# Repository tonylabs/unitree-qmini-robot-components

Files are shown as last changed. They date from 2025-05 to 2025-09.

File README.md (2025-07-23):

# Unitree Qmini Robot Resources

## 说明

这里不是 Unitree Qmini 机器人的官方 Git 资源库，点击[这里](https://github.com/unitreerobotics/Qmini) 访问官方 Repo.

本仓库包含了**修改**后 Unitree Qmini 机器人打印件，例如将部分螺丝孔位增加了倒角，减少不必要的打印支撑。和其他改装件，和部分为 Qmini 专门设计的 PCB。

### 站立支架

#### 所需材料

- [2040 铝合金型材 x 5](https://www.misumi.com.cn/vona2/detail/110310158399/?ProductCode=LCFB6-2040-200-TPW) 长度最短不小于100mm，两端加工螺纹。
- [M6 x 25mm x 20](https://item.taobao.com/item.htm?id=596366591280&skuId=4312388615153)
- M3 x 14 x 8
- M3 螺母 x 8

## Qmini 结构

```mermaid
flowchart TD
    subgraph "Qmini Robot"
        Body["Base Link"]
        %% Left Leg (LL)
        LL_HipYaw["LL Hip Yaw"]
        LL_HipRoll["LL Hip Roll"]
        LL_HipPitch["LL Hip Pitch"]
        LL_Knee["LL Knee"]
        LL_Ankle["LL Ankle"]
        
        %% Right Leg (RL)
        RL_HipYaw["RL Hip Yaw"]
        RL_HipRoll["RL Hip Roll"]
        RL_HipPitch["RL Hip Pitch"]
        RL_Knee["RL Knee"]
        RL_Ankle["RL Ankle"]
        
        %% Left Leg Connections
        Body --> LL_HipYaw
        LL_HipYaw --> LL_HipRoll
        LL_HipRoll --> LL_HipPitch
        LL_HipPitch --> LL_Knee
        LL_Knee --> LL_Ankle
        
        %% Right Leg Connections
        Body --> RL_HipYaw
        RL_HipYaw --> RL_HipRoll
        RL_HipRoll --> RL_HipPitch
        RL_HipPitch --> RL_Knee
        RL_Knee --> RL_Ankle
    end
```

### How to use the qmini_description

1. Navigate to your workspace:

```bash
$ sudo apt-get install python3-colcon-common-extensions
$ pip install catkin_pkg
$ cd /home/ubuntu/Documents/GitHub/unitree-qmini-robot-components/qmini_description
```

2. Build the package:

```bash
$ colcon build --packages-select qmini_description
```

3. Source the workspace:

```bash
$ source install/setup.bash
```

4. Launch the robot description:

```bash
$ ros2 launch qmini_description view_qmini.launch.py
```

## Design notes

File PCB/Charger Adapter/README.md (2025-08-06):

## Charger Adapter for Qmini Robot

### BOM

- J1, J2: [XT60PW-M](https://item.taobao.com/item.htm?id=934094991009&skuId=5824271752085)
- J3: [PJ-202A](https://item.taobao.com/item.htm?id=696211501043)
- J4, J5: [HF-B01M-11P-R1-A](https://item.taobao.com/item.htm?id=779219267835)
- C1~C4: 100uF 25V 6.3 x 5.4mm
- D1: [SMCJ45A](https://item.taobao.com/item.htm?id=608465785790)
- M1~M4: [SMTSO-M3-1.5ET](https://item.taobao.com/item.htm?id=626464596047&skuId=4448515665378)

### PCB Manufacturer

- Board Dimensions: 8.90 cm x 4.30 cm
- Board Thickness: 1.6mm ~ 2mm

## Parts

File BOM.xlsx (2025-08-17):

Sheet: 3D Print
 | Material | Infill | Insert | Printing Hours | Price
BODY
Battery Pack Bottom | ABS-HF | 15% |  | 13 | ¥0.00
Battery Pack 电池仓 | ABS-HF | 15% | M4 (6x6) x 8 | 35 | ¥0.00
Frame Core | Polymaker HT-PLA | 20% | M4 x 10 | M3 x 4 | 72 | ¥0.00
Frame Front Bottom 前端风扇安装件 | Polymaker HT-PLA | 100% | M3 x 6 | 0 | ¥0.00
Frame Top | Polymaker HT-PLA | 20% | M5 x 4 |  | ¥0.00
Handle |  |  |  |  | ¥0.00
Neck Actuator Mount | ABS-HF |  |  | 8 | ¥130.00
Raspberry Pi 4B Mount | ABS-HF |  |  | 6 | ¥0.00
Yaw Bottom Limit | ABS-HF |  |  | 2.1 | ¥0.00
Yaw Top | ABS-HF |  | M3 x 2 | 2.5 | ¥0.00
 |  |  |  |  | ¥0.00
 |  |  |  |  | ¥0.00
 |  |  |  |  | ¥0.00
 |  |  |  |  | ¥0.00
HIP
Hip Gear Left | Nylon 3201PA-F | 100% |  |  | ¥30.00
Hip Gear Right | Nylon 3201PA-F | 100% |  |  | ¥30.00
Hip Joint Roll Left | Nylon 3201PA-F | 100% |  |  | ¥178.00
Hip Joint Roll Right | Nylon 3201PA-F | 100% |  |  | ¥178.00
Hip Joint Mount Left | Resin-X | 40% | M4 x 4 | 13 | ¥38.00
Hip Joint Mount Right | Resin-X | 40% | M4 x 4 | 13 | ¥38.00
Hip Joint Yaw Left | Resin-X | 40% | M5 x 1 | 8 | ¥25.64
Hip Joint Yaw Right | Resin-X | 40% | M5 x 1 | 8 | ¥25.64
LEG
Lower Leg Right Cover | ABS-HF |  |  | 4.3 | ¥0.00
Lower Leg Right | ABS-HF / Nylon 3201PA-F |  |  | 9.4 | ¥353.00
Upper Leg Right Cover | ABS-HF |  |  | 11.55 | ¥0.00
Upper Leg Right | Resin-X |  |  | 0 | ¥126.89
Lower Leg Left Cover | ABS-HF |  |  | 4.3 | ¥0.00
Lower Leg Left | ABS-HF / Nylon 3201PA-F |  |  | 9.4 | ¥353.00
Upper Leg Left Cover | ABS-HF |  |  | 11.55 | ¥0.00
Upper Leg Left | Resin-X |  |  | 0 | ¥126.89
FOOT
Right Foot A | ABS-HF |  | M3 x 3 | 10.36 | ¥0.00
Right Foot B | ABS-HF |  |  | 5.4 | ¥0.00
Right Foot Pad 足底 | Resin |  |  | 0 | ¥145.00
Left Foot A | ABS-HF |  | M3 x 3 | 10.36 | ¥0.00
Left Foot B | ABS-HF |  |  | 5.4 | ¥0.00
Left Foot Pad 足底 | Resin |  |  | 0 | ¥145.00
PANEL
Panel Top Front | Resin-X | 100% | M3 x 2 | 0 | ¥198.00
Panel Top Rear | Resin-X | 100% |  | 0 | ¥143.00
Antenna Left | Resin-X | 100% |  |  | ¥24.00
Antenna Right | Resin-X | 100% |  |  | ¥24.00
 |  |  |  | 262.62 | ¥2312.06

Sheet: BOM
ITEM | SPECS | LINK | NOTES | QUANTITY | PRICE | SUBTOTAL
BODY
GO-M8010-6 | 24V | https://detail.tmall.com/item.htm?id=679335252560&skuId=5079135404284 |  | 11 | 550 | ¥6050.00
BODY
M5 热熔螺母 | M5 x 10 OD 7 | https://detail.tmall.com/item.htm?id=899448134936&skuId=5754304832006 | Frame Top | Hip Motor Mount | 4 | 0.15 | ¥0.60
M4 热熔螺母 | M4 x 10 OD 6 | https://detail.tmall.com/item.htm?id=899448134936&skuId=5798756972352 | Frame Top | Frame Core | Battery Pack | Hip Motor Mount | 28 | 0.2 | ¥5.60
M3 热熔螺母 | M3 x 4 OD 5 | https://item.taobao.com/item.htm?id=593581996419&skuId=4189077672129 | Frame Core | Front Bottom Fan Mount | IMU Mount | 12 | 0.2 | ¥2.40
不锈钢衬套 | Φ6 x 8 x 35 | https://detail.tmall.com/item.htm?id=822545298024&skuId=5702459126386 |  | 2 | 1.42 | ¥2.84
粒片螺丝 | M3.5 x 8 | https://item.taobao.com/item.htm?id=537967383377&skuId=3212738635362 | 髋关节电机安装座 | 顶部 YAW 轴电机 | 24 | 0.3 | ¥7.20
粒片螺丝 | M3.5 x 16 |  | 上身电机上盖底部限位 | 6 | 0.3 | ¥1.80
粒片螺丝 | M4 x 16 | https://item.taobao.com/item.htm?id=537967383377&skuId=5461813862733 | 髋关节电机安装座 | 8 | 0.3 | ¥2.40
FHCS 螺丝 | M4 x 12 平头 | https://item.taobao.com/item.htm?id=525468794969&skuId=3127568831102 | 摆驱动齿轮 | 12 | 0.3 | ¥3.60
SHCS 螺丝 | M4 x 12 杯头 | https://item.taobao.com/item.htm?id=525468794969&skuId=3127568831102 | 电机抱箍 | 4 | 0.3 | ¥1.20
SHCS 螺丝 | M4 x 16 杯头 | https://item.taobao.com/item.htm?id=529627939342&skuId=3165003331293 | 电池底部支撑件 | 机身上下主体 | 顶部 YAW 轴电机 | 侧摆电机 | 15 | 0.36 | ¥5.40
SHCS 螺丝 | M4 x 18 杯头 | https://item.taobao.com/item.htm?id=529627939342&skuId=3206368205626 | 电机抱箍 | 4 | 0.36 | ¥1.44
SHCS 螺丝 | M4 x 20 杯头 | https://item.taobao.com/item.htm?id=529627939342&skuId=3200246575353 | 主骨架与电池仓连接 | 前端风扇安装件 | 6 | 0.36 | ¥2.16
SHCS 螺丝 | M4 x 25 杯头 | https://item.taobao.com/item.htm?id=529627939342&skuId=3165003331294 | 机身上下主体 | 9 | 0.48 | ¥4.32
SHCS 螺丝 | M3 x 10 杯头 | https://item.taobao.com/item.htm?id=38977230812&skuId=3165007311199 | 4010 DC Fan | 4 | 0.28 | ¥1.12
SHCS 螺丝 | M3 x 14 杯头 | https://item.taobao.com/item.htm?id=38977230812&skuId=3165007311200 | 4010 DC Fan | 4 | 0.28 | ¥1.12
平面滚针轴承 | BA0619 | https://detail.tmall.com/item.htm?id=625077079266&skuId=5611160825675 | Frame Core | 2 | 3 | ¥6.00
636ZZ 轴承 | 6 x 22 x 7 | https://item.taobao.com/item.htm?id=652062390391&skuId=4698920756210 | Frame Core | 侧摆 | 4 | 6.5 | ¥26.00
塞打螺栓 | ￠6 x M5 x 16 | https://detail.tmall.com/item.htm?id=610905186565&skuId=5148221219880 | Frame Core | 2 | 1.062 | ¥2.12
塞打螺栓 | ￠6 x M5 x 55 | https://detail.tmall.com/item.htm?id=610905186565&skuId=4925270516930 | 侧摆 | 2 | 1.585 | ¥3.17
垫片 | 5.2 x D10 x 2 黑色 | https://item.taobao.com/item.htm?id=667085311743&skuId=4865635364512 | 侧摆 | 2 | 0.46 | ¥0.92
船形开关 | KCD1-104 | https://item.taobao.com/item.htm?id=577536722051 | 2档 | 1 | 1.12 | ¥1.12
轴流风扇 | 4010 24V DC | https://item.taobao.com/item.htm?id=611636440997&skuId=4310799149744 |  | 2 | 8 | ¥16.00
USB 转 485 | 四通道 | https://detail.tmall.com/item.htm?id=679335252560&skuId=5978377674682 |  | 1 | 199 | ¥199.00
动力线 | 16awg | https://detail.tmall.com/item.htm?id=679335252560&skuId=5136048959263 |  | 4 | 49 | ¥196.00
Raspberry Pi | 4B | https://detail.tmall.com/item.htm?id=679335252560&skuId=5079135404284 |  | 1 | 377 | ¥377.00
电池 | GO1-BT03 标准版 | https://detail.tmall.com/item.htm?id=654533678350&skuId=4892505606177 |  | 1 | 1999 | ¥1999.00
充电器 | GO1 | https://detail.tmall.com/item.htm?id=654533678350&skuId=5036835474357 |  | 1 | 600 | ¥600.00
IMU | N100 不带外壳 | https://detail.tmall.com/item.htm?id=645061129098&skuId=4648099525532 |  | 1 | 265 | ¥265.00
LEG
粒片螺丝 | M3.5 x 8 | https://item.taobao.com/item.htm?id=537967383377&skuId=3212738635362 | M8010 电机 | 50 | 0.3 | ¥15.00
粒片螺丝 | M3.5 x 12 | https://item.taobao.com/item.htm?id=537967383377&skuId=3212738635365 | 脚踝电机侧盖 | 50 | 0.3 | ¥15.00
SHCS 螺丝 | M4 x 16 杯头 | https://item.taobao.com/item.htm?id=529627939342&skuId=3165003331293 | 大、小腿连接 | 12 | 0.36 | ¥4.32
离心风扇 | 3010 24V DC 滚珠轴承 | https://item.taobao.com/item.htm?id=566323233973&skuId=5212591909140 |  | 4 | 16.5 | ¥66.00
动力线 | 16awg | https://detail.tmall.com/item.htm?id=679335252560&skuId=5136048959263 |  | 4 | 49 | ¥196.00
足端
M3 热熔螺母 | M3 x 7 OD 4.2 | https://detail.tmall.com/item.htm?id=899448134936&skuId=5922977711804 | Foot A | 6 | 0.2 | ¥1.20
SHCS 螺丝 | M3 x 25 杯头 | https://item.taobao.com/item.htm?id=38977230812&skuId=3200123895845 |  | 6 | 0.31 | ¥1.86
粒片螺丝或 FHCS 平头 | M4 x 16 | https://item.taobao.com/item.htm?id=537967383377&skuId=5461813862733 https://item.taobao.com/item.htm?id=525468794969&skuId=3127568831104 | 足端连接电机转轴 | 12 | 0.3 | ¥3.60
足底 |  |  | TPU 或柔性树脂 | 2 | 0 | ¥0.00
PANEL
M3 热熔螺母 | M3 x 7 OD 4.2 | https://detail.tmall.com/item.htm?id=899448134936&skuId=5922977711804 | Front Panel | 2 | 0.2 | ¥0.40
粒片螺丝 | M3.5 x 12 | https://item.taobao.com/item.htm?id=537967383377&skuId=3212738635365 | 顶盖 | 4 | 0.3 | ¥1.20
SHCS 螺丝 | M3 x 10 杯头 | https://item.taobao.com/item.htm?id=38977230812&skuId=3165007311199 | 天线 | 脸部 | 4 | 0.28 | ¥1.12
SHCS 螺丝 | M5 x 16 杯头 | https://item.taobao.com/item.htm?id=35431215248&skuId=3165685753062 | 提手 | 2 | 0.21 | ¥0.42
其他
波纹软管 |  |  |  | 1 | 5 | ¥5.00
站立支架
2040 型材 | 经济型欧标槽宽 6mm | https://www.misumi.com.cn/vona2/detail/110310158399/?ProductCode=LCFB6-2040-200-TPW |  | 5 | 13.19 | ¥65.95
BHCS 螺丝 | M6 x 25 | https://item.taobao.com/item.htm?id=596366591280&skuId=4312388615153 | 打印件连接 2040 型材 | 20 | 0.95 | ¥19.00
BHCS 螺丝 | M5 x 8 |  |  | 16 |  | ¥0.00
FHCS 螺丝 | M3 x 14 杯头 |  |  | 8 |  | ¥0.00
M3 螺母 |  |  |  | 8 |  | ¥0.00
 |  |  |  |  |  | ¥0.00
 |  |  |  |  |  | ¥0.00
 |  |  |  |  |  | ¥10180.60

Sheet: Wiring
连接 | 线径 | 长度 | 连接器 | 说明
大腿 | 16 AWG | 58cm | XT30(2+2) | 左电机 0 或右电机 0 连接至分电板
小腿 | 16 AWG | 25cm | XT30(2+2) | 左电机 1 或右电机 1 连接至左电机 2 或右电机 2

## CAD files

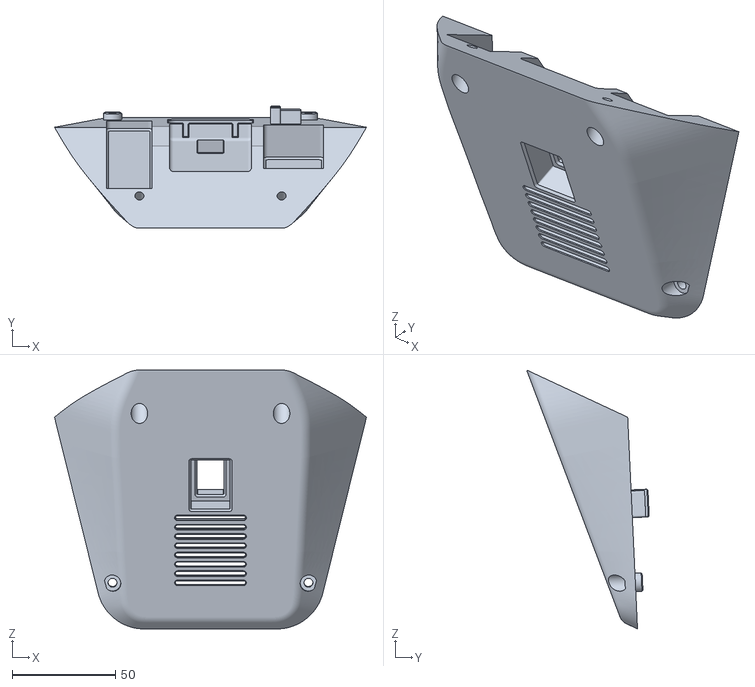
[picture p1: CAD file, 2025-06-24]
Print/Body/Battery Pack/DJI TB50-TB55/Battery Pack Bottom with 4010 Fan.stl
151.3 x 59.4 x 125.5

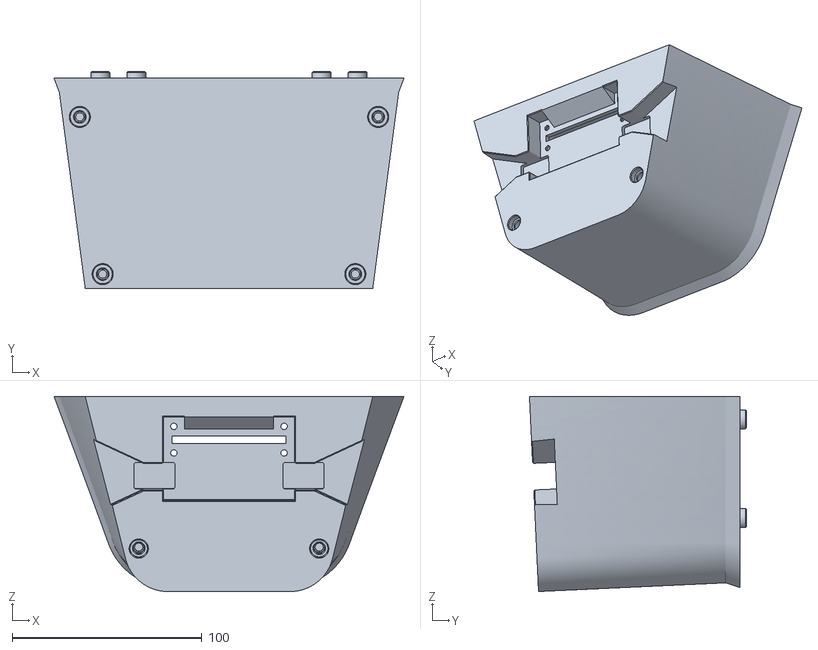
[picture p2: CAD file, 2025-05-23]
Print/Body/Battery Pack/GO1/Battery Pack GO1.stl
184.2 x 114.3 x 102.7

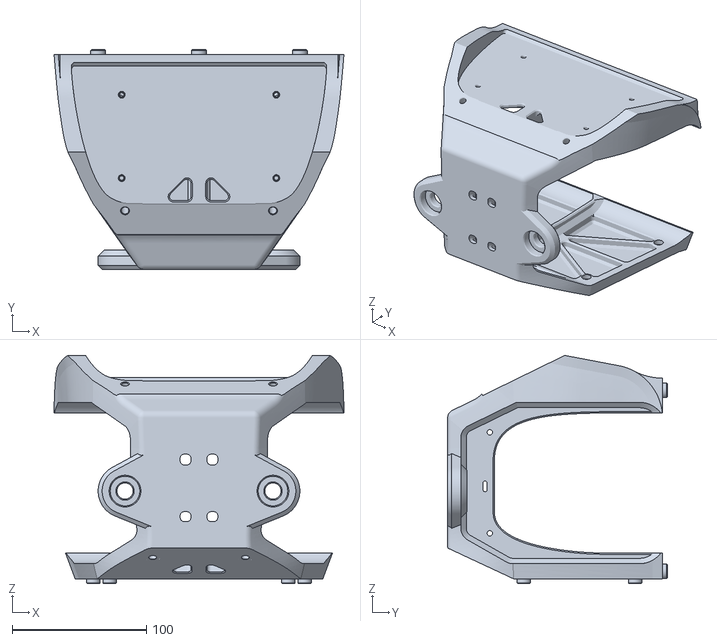
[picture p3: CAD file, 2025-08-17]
Print/Body/Frame Core.stl
215.6 x 163.3 x 169.7

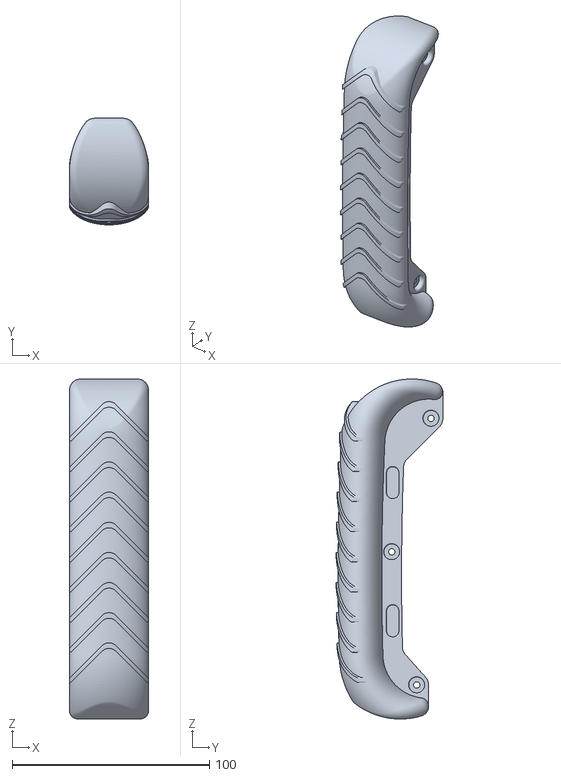
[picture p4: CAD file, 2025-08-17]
Print/Foot/Foot Pad x 2.stl
40.0 x 54.1 x 172.2

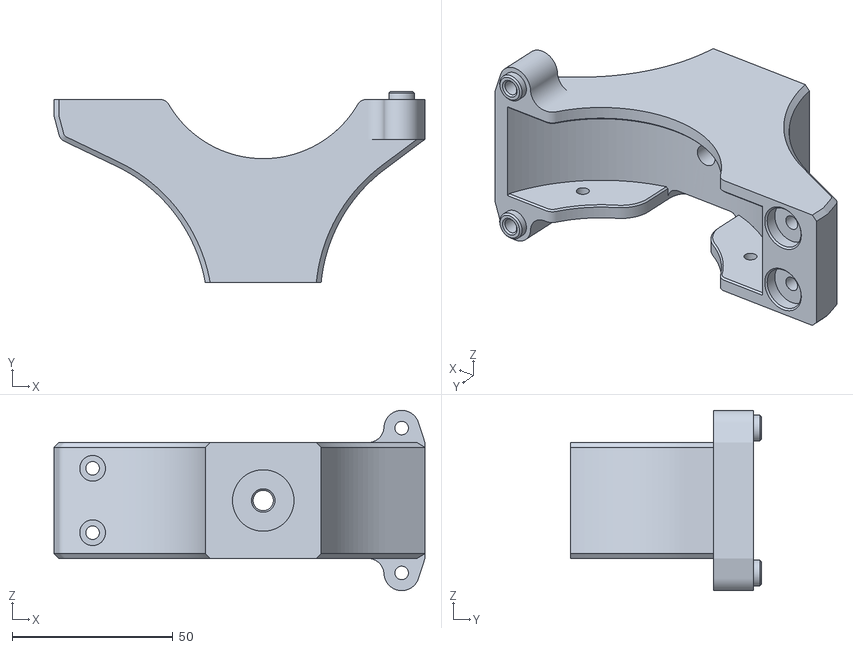
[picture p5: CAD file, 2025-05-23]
Print/Hip/Hip Joint Yaw Right.stl
115.2 x 59.4 x 56.0

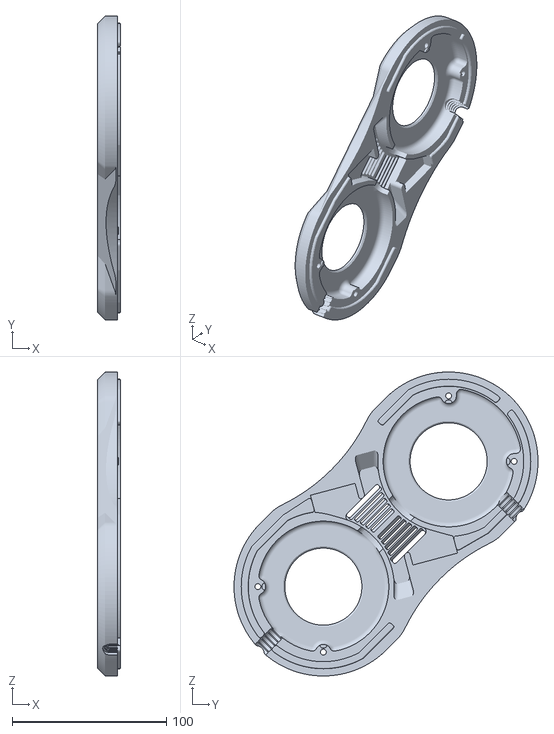
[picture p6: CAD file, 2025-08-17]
Print/Leg/Hollow - Upper Leg Right Cover.stl
15.0 x 197.3 x 197.3

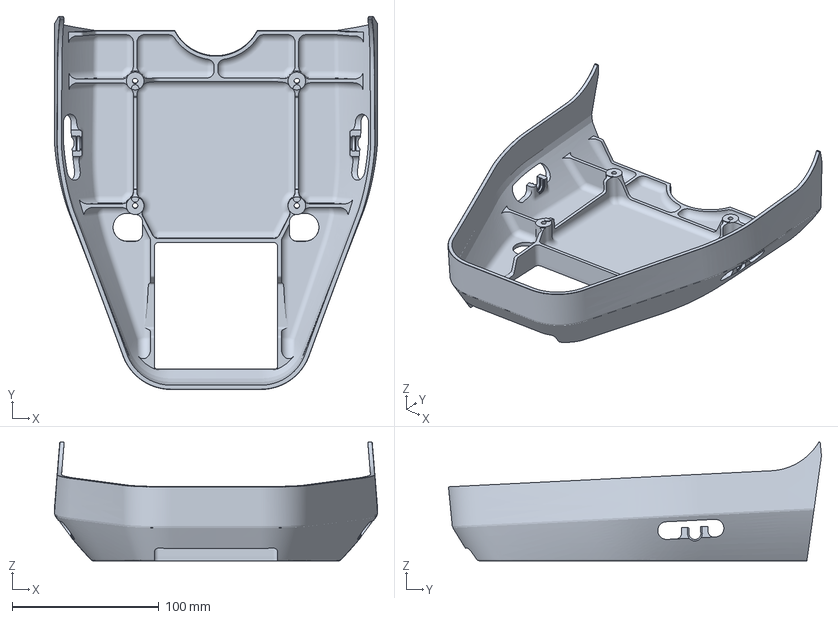
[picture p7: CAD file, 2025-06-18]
Print/Panel/Bambu Studio/Panel Top Rear.3mf
219.9 x 253.8 x 80.9 mm

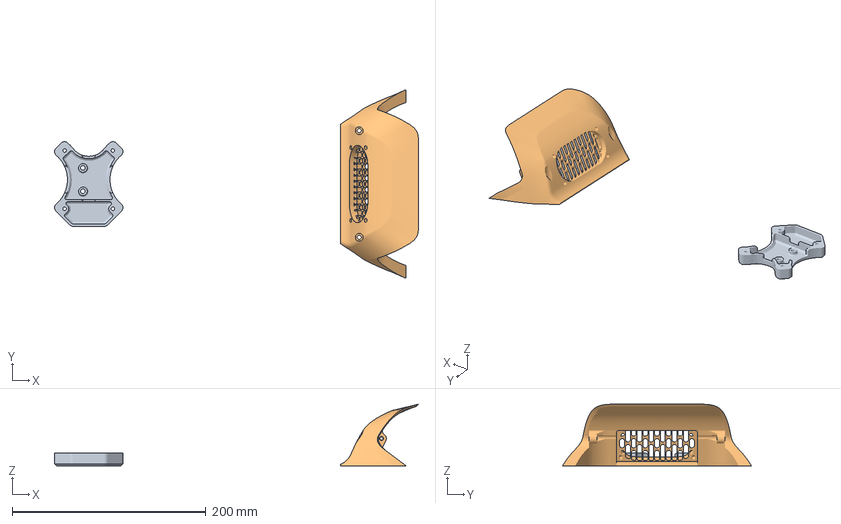
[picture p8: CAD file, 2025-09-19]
Print/Qmini - Bambu Studio.3mf
375.7 x 194.9 x 63.6 mm
Hip_Yaw_Top
Front Bottom

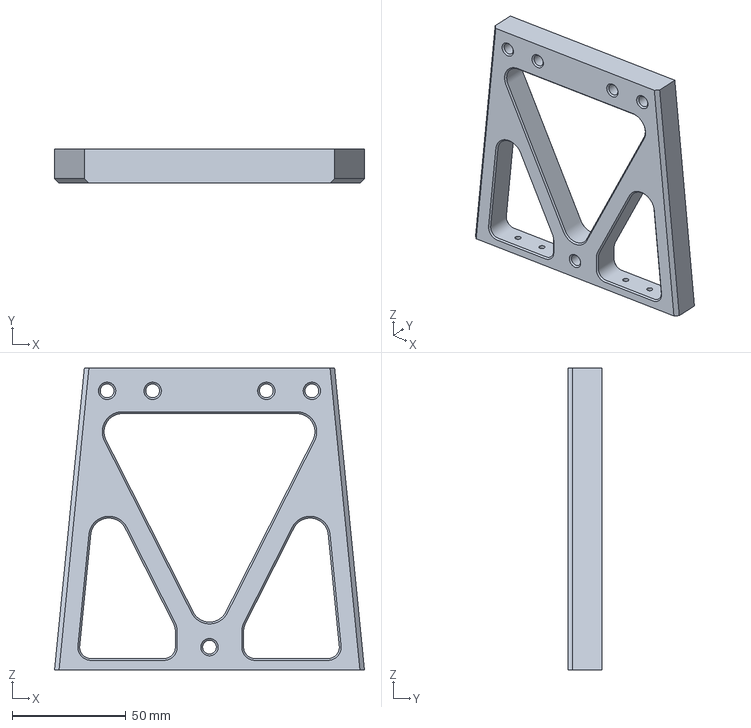
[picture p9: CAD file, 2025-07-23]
Print/Standing Frame/Standing Frame A x 2.3mf
136.1 x 15.0 x 132.6 mm

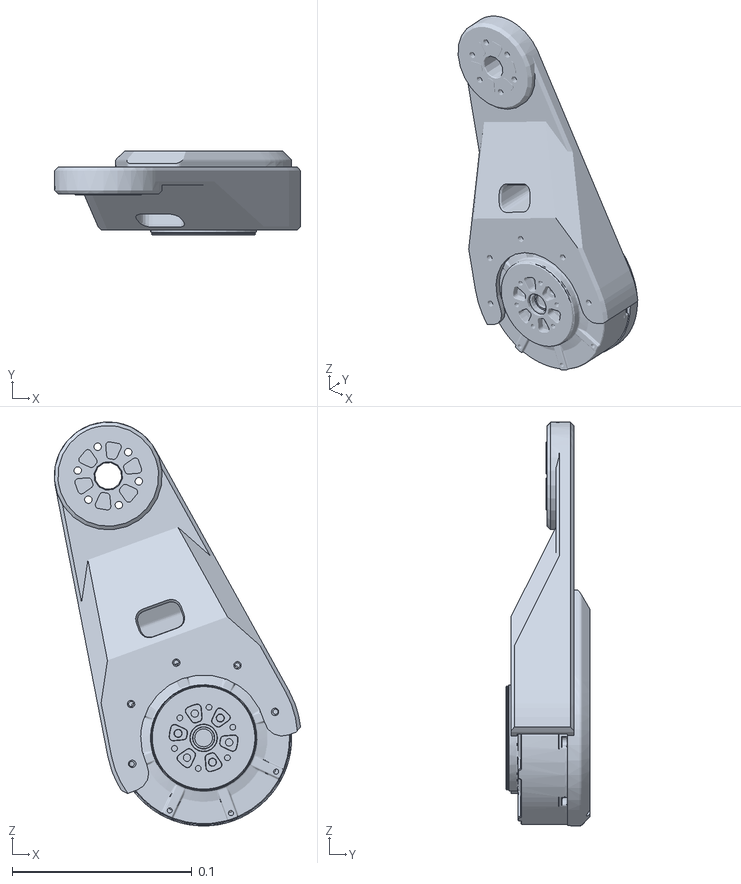
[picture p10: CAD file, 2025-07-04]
qmini_description/meshes/RL_knee.STL
0.137 x 0.0468 x 0.225

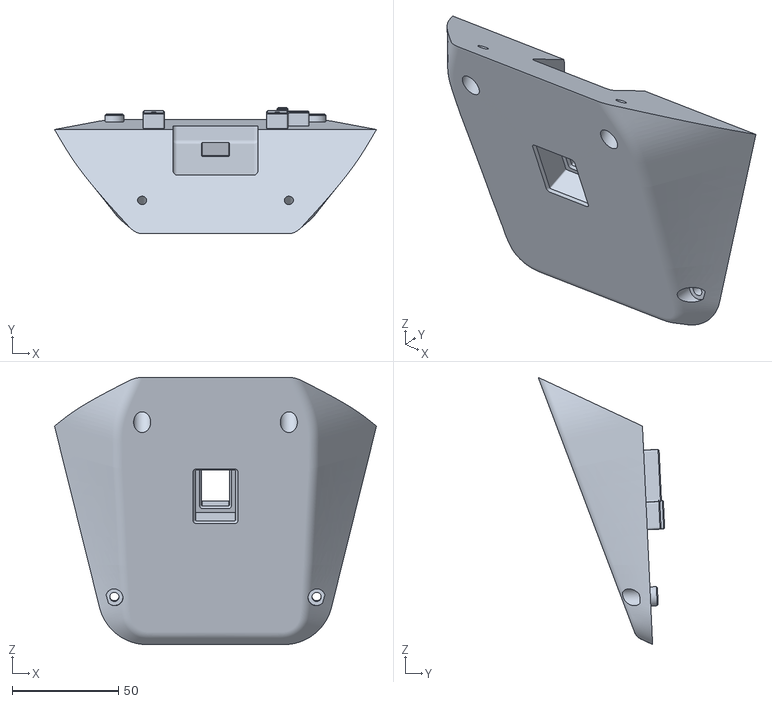
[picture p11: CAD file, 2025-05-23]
Print/Body/Battery Pack/GO1/Battery Pack Bottom GO1.stl
151.3 x 59.4 x 125.5

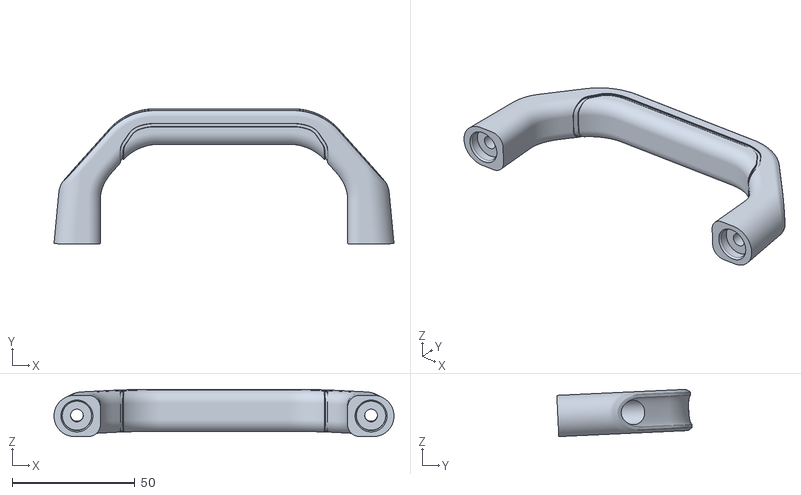
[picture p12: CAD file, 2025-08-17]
Print/Body/Handle.stl
138.7 x 55.2 x 19.3

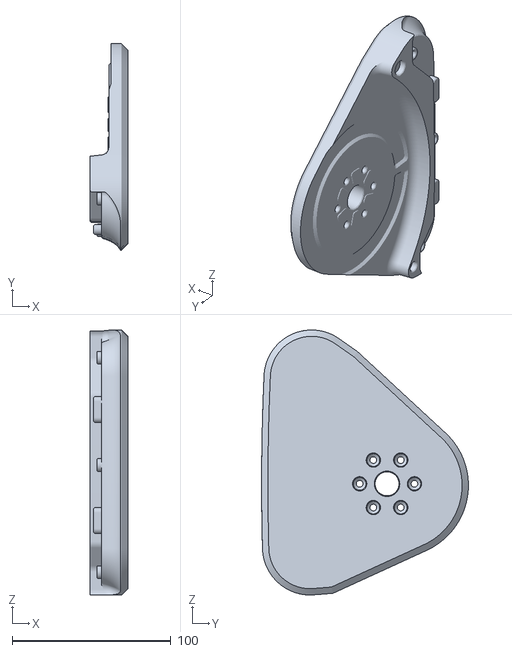
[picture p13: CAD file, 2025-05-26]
Print/Foot/Left Foot A.stl
23.8 x 130.2 x 166.8

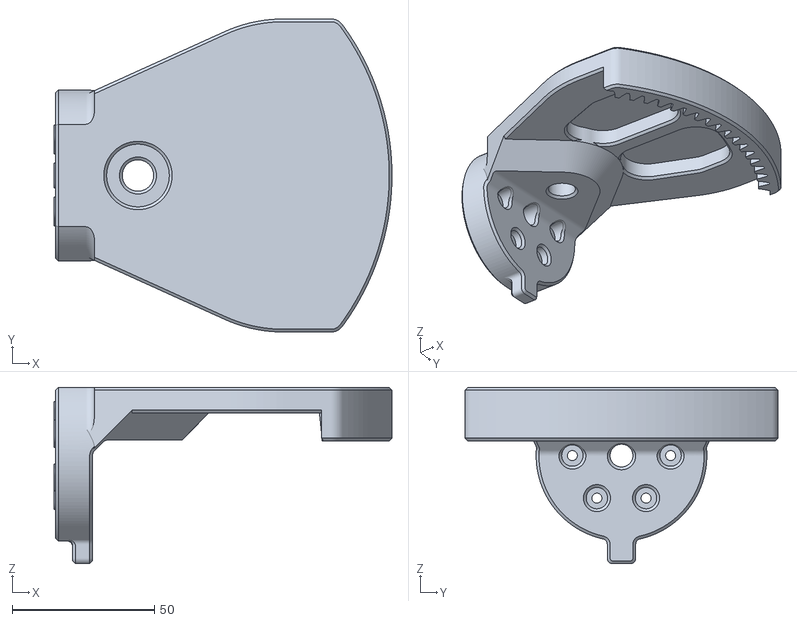
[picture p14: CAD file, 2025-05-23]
Print/Hip/Hip Joint Roll Right.stl
118.7 x 110.0 x 62.0

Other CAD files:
PCB/Charger Adapter/qmini-charger-adapter.step
Print/Panel/Panel Top Rear.step
Print/Leg/Hollow - Upper Leg Left Cover.stl
Print/Panel/Panel Front.step
Print/Body/Frame Front Bottom.stl
Print/Body/Frame Top.stl
Print/Body/IMU N100 Mount.stl
Print/Body/Jetson Orin Nano Mount A.stl
Print/Body/Jetson Orin Nano Mount B.stl
Print/Body/Neck Actuator Mount.stl
Print/Body/Raspberry Pi 4B Mount.stl
Print/Body/Yaw Bottom Limit.stl
Print/Foot/Left Foot B.stl
Print/Foot/Right Foot A.stl
Print/Foot/Right Foot B.stl
Print/Hip/Hip Gear Left.stl
Print/Hip/Hip Gear Right.stl
Print/Hip/Hip Joint Mount Left.stl
Print/Hip/Hip Joint Mount Right.stl
Print/Hip/Hip Joint Roll Left.stl
Print/Hip/Hip Joint Yaw Left.stl
Print/Leg/Hollow - Lower Leg Left Cover.stl
Print/Leg/Hollow - Lower Leg Right Cover.stl
Print/Leg/Lower Leg Left Cover.stl
Print/Leg/Lower Leg Left.stl
Print/Leg/Lower Leg Right Cover.stl
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

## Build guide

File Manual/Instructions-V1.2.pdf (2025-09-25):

# 宇树 Qmini 双足机器人

# 本体组装制作说明 V1.2

## 1.1 机身主体零部件

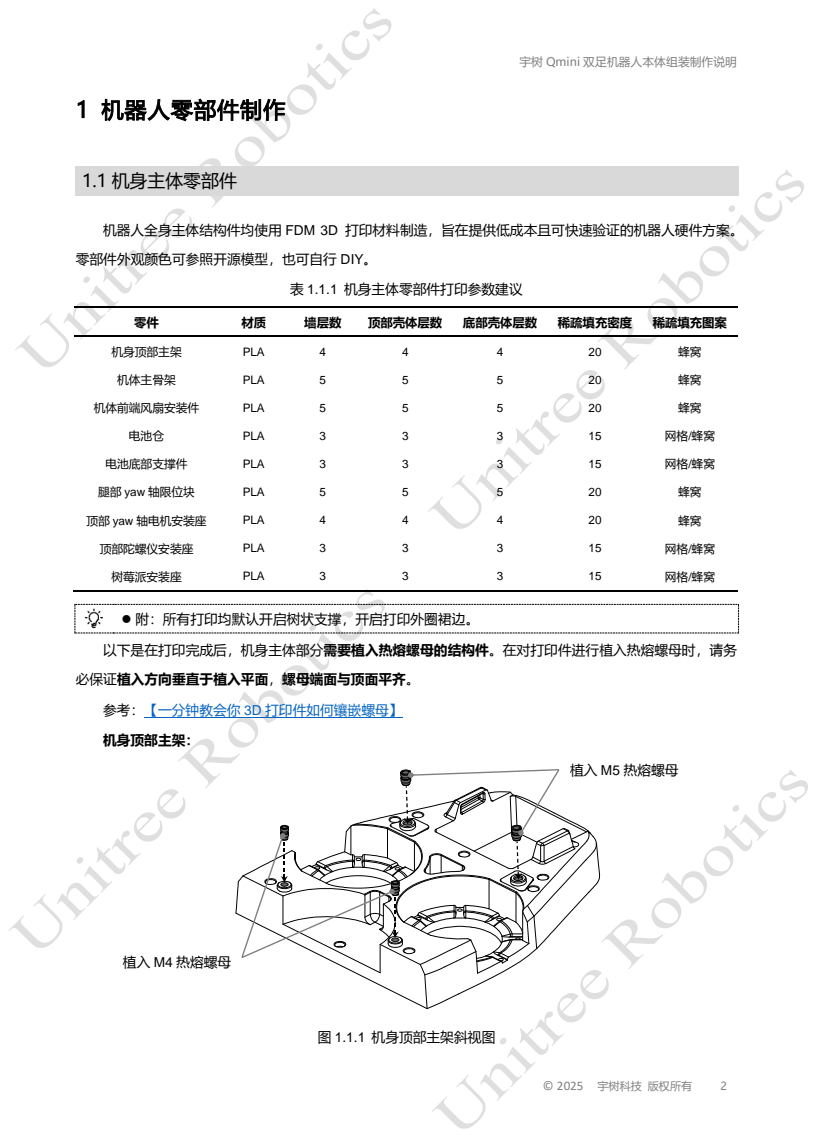
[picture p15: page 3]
© 2025 宇树科技 版权所有; 表 1.1.1 机身主体零部件打印参数建议; 墙层数; 顶部壳体层数; 底部壳体层数; 稀疏填充密度; 稀疏填充图案; 机身顶部主架; PLA; 机体主骨架; 机体前端风扇安装件; 电池仓; 电池底部支撑件; 腿部 yaw 轴限位块; 顶部 yaw 轴电机安装座; 顶部陀螺仪安装座; 树莓派安装座; ⚫ 附：所有打印均默认开启树状支撑，开启打印外圈裙边。; 必保证植入方向垂直于植入平面，螺母端面与顶面平齐。; 机身顶部主架：; 图 1.1.1 机身顶部主架斜视图; 植入 M4 热熔螺母; 植入 M5 热熔螺母

宇树 Qmini 双足机器人本体组装制作说明

机器人全身主体结构件均使用 FDM 3D 打印材料制造，旨在提供低成本且可快速验证的机器人硬件方案。

零部件外观颜色可参照开源模型，也可自行 DIY。

以下是在打印完成后，机身主体部分需要植入热熔螺母的结构件。在对打印件进行植入热熔螺母时，请务

参考：【一分钟教会你 3D 打印件如何镶嵌螺母】 (https://www.bilibili.com/video/BV1U14y1Q7qn/?share_source=copy_web&vd_source=937fc9)

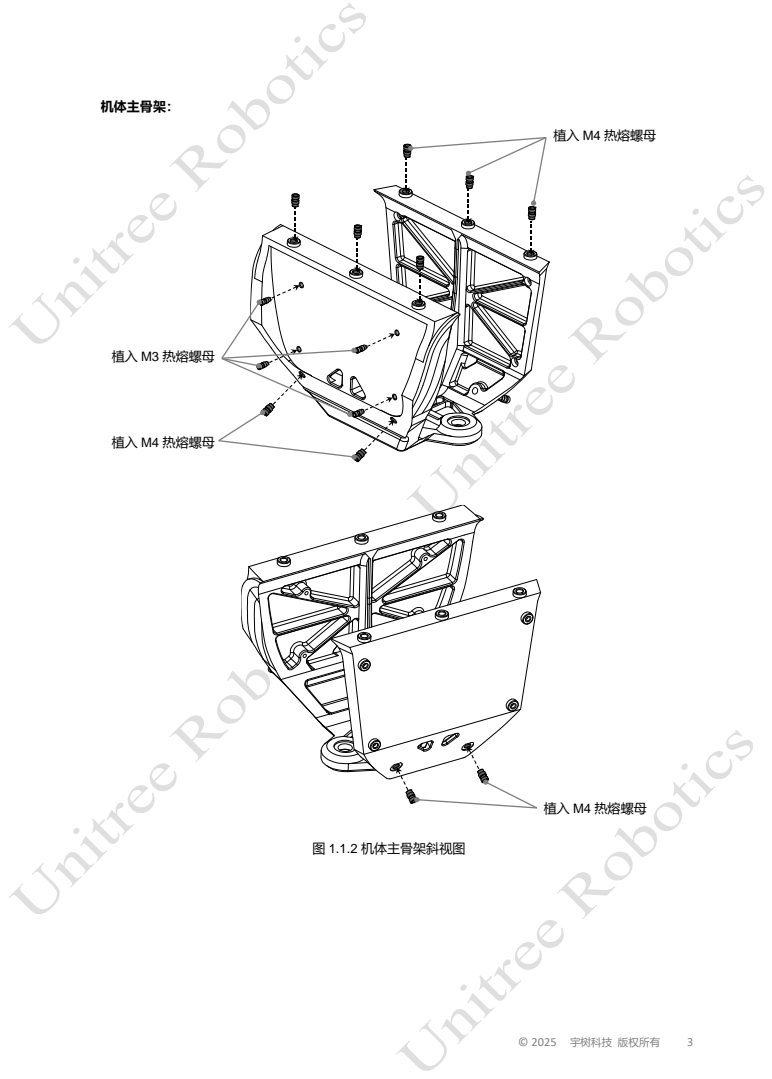
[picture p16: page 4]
机体主骨架：; 图 1.1.2 机体主骨架斜视图; 植入 M4 热熔螺母; 植入 M3 热熔螺母

## 1.2 腿部零部件

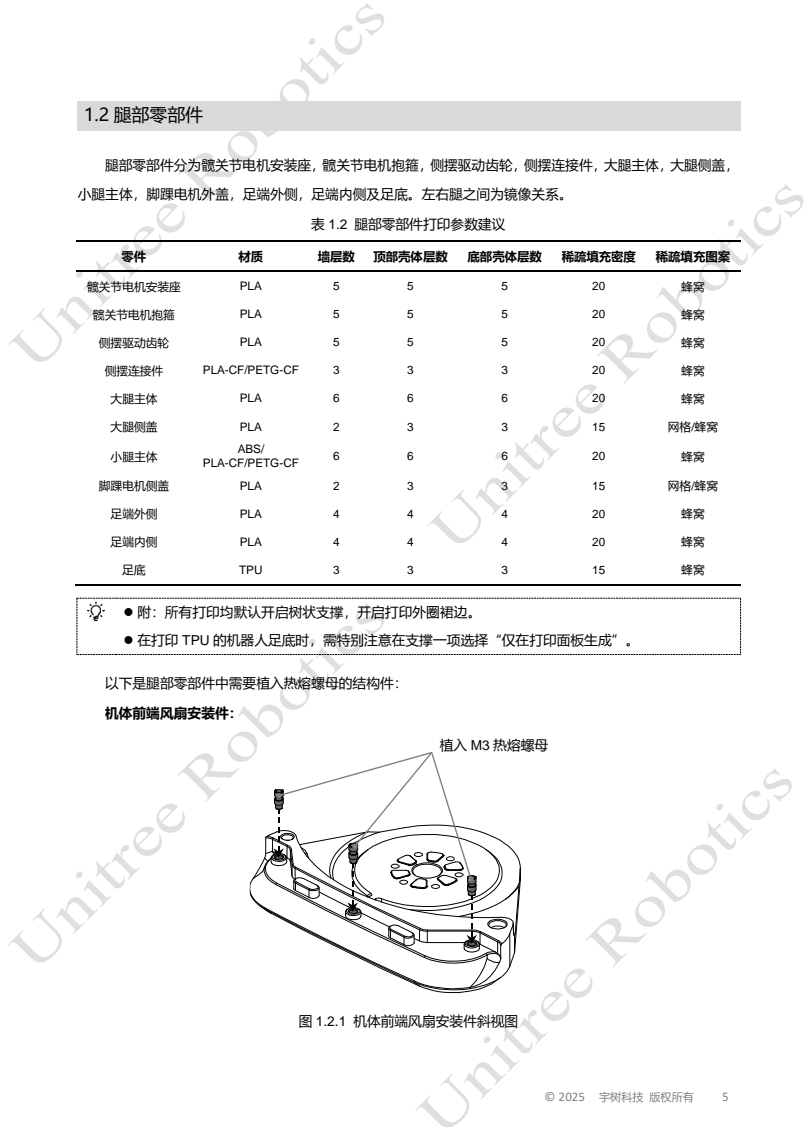
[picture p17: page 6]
表 1.2 腿部零部件打印参数建议; 墙层数; 顶部壳体层数; 底部壳体层数; 稀疏填充密度; 稀疏填充图案; 髋关节电机安装座; PLA; 髋关节电机抱箍; 侧摆驱动齿轮; 侧摆连接件; PLA-CF/PETG-CF; 大腿主体; 大腿侧盖; 小腿主体; ABS/; 脚踝电机侧盖; 足端外侧; 足端内侧; TPU; 以下是腿部零部件中需要植入热熔螺母的结构件：; 机体前端风扇安装件：; 图 1.2.1 机体前端风扇安装件斜视图; 植入 M3 热熔螺母

腿部零部件分为髋关节电机安装座，髋关节电机抱箍，侧摆驱动齿轮，侧摆连接件，大腿主体，大腿侧盖，

小腿主体，脚踝电机外盖，足端外侧，足端内侧及足底。左右腿之间为镜像关系。

⚫ 附：所有打印均默认开启树状支撑，开启打印外圈裙边。
⚫ 在打印 TPU 的机器人足底时，需特别注意在支撑一项选择“仅在打印面板生成”。

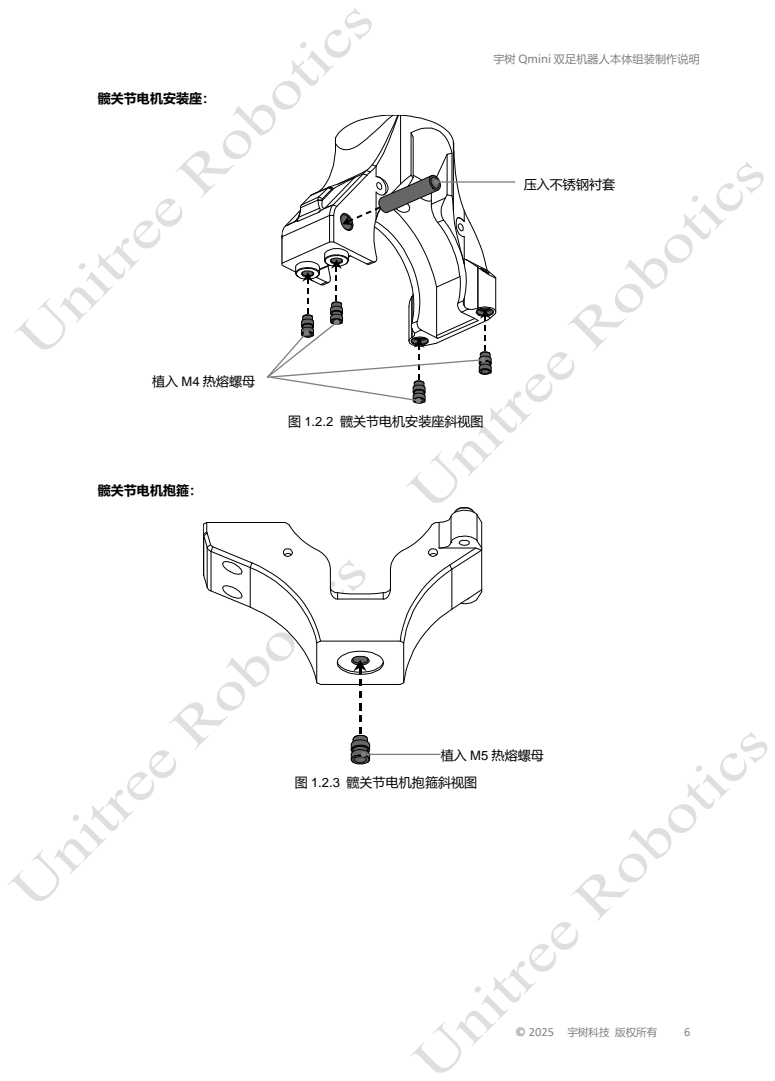
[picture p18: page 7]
髋关节电机安装座：; 图 1.2.2 髋关节电机安装座斜视图; 髋关节电机抱箍：; 图 1.2.3 髋关节电机抱箍斜视图; 植入 M4 热熔螺母; 压入不锈钢衬套; 植入 M5 热熔螺母

## 1.3 外观装饰件和其他结构件

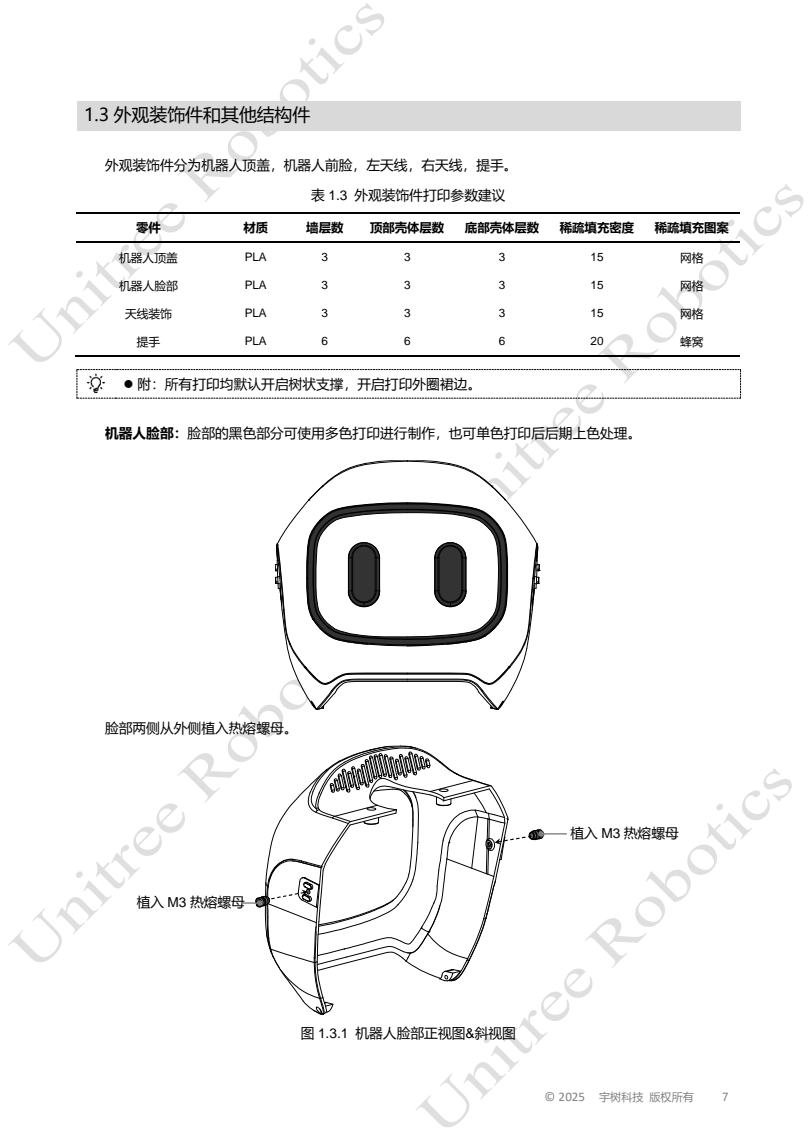
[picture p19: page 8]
表 1.3 外观装饰件打印参数建议; 墙层数; 顶部壳体层数; 底部壳体层数; 稀疏填充密度; 稀疏填充图案; 机器人顶盖; PLA; 机器人脸部; 天线装饰; ⚫ 附：所有打印均默认开启树状支撑，开启打印外圈裙边。; 脸部两侧从外侧植入热熔螺母。; 图 1.3.1 机器人脸部正视图&斜视图; 植入 M3 热熔螺母

外观装饰件分为机器人顶盖，机器人前脸，左天线，右天线，提手。

机器人脸部：脸部的黑色部分可使用多色打印进行制作，也可单色打印后后期上色处理。

## 2.1 电机系统框图

## 2.2 机身主体组装

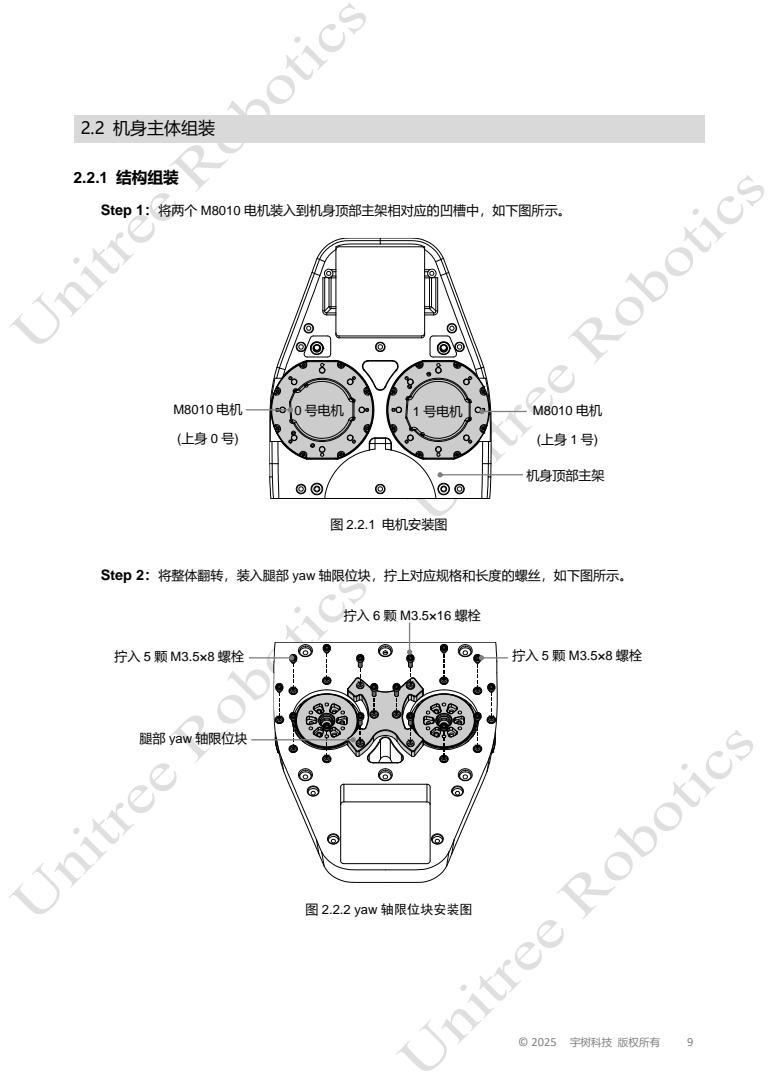
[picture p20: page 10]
2.2.1 结构组装; 图 2.2.1 电机安装图; 图 2.2.2 yaw 轴限位块安装图; 0 号电机; 1 号电机; 机身顶部主架

Step 1：将两个 M8010 电机装入到机身顶部主架相对应的凹槽中，如下图所示。

Step 2：将整体翻转，装入腿部 yaw 轴限位块，拧上对应规格和长度的螺丝，如下图所示。

腿部 yaw 轴限位块

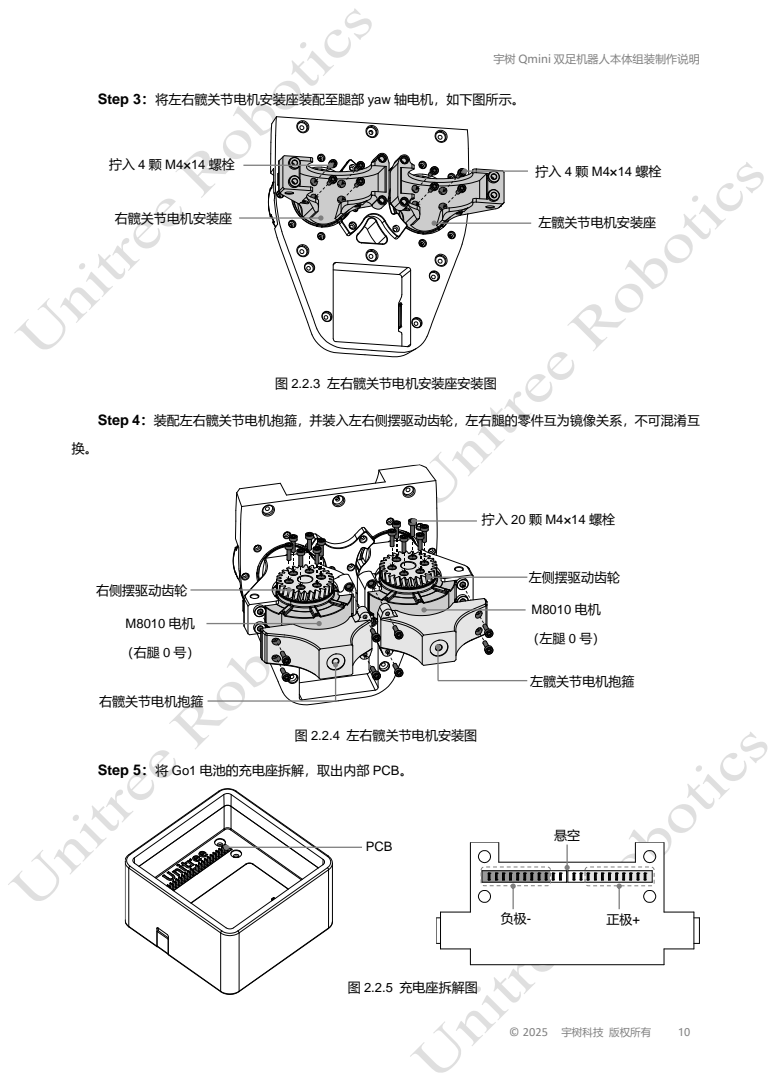
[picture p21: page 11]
图 2.2.3 左右髋关节电机安装座安装图; 图 2.2.4 左右髋关节电机安装图; 左髋关节电机安装座; 右髋关节电机安装座; 右侧摆驱动齿轮; 左侧摆驱动齿轮; 右髋关节电机抱箍; 左髋关节电机抱箍; PCB; 图 2.2.5 充电座拆解图

Step 3：将左右髋关节电机安装座装配至腿部 yaw 轴电机，如下图所示。

Step 4：装配左右髋关节电机抱箍，并装入左右侧摆驱动齿轮，左右腿的零件互为镜像关系，不可混淆互

Step 5：将 Go1 电池的充电座拆解，取出内部 PCB。

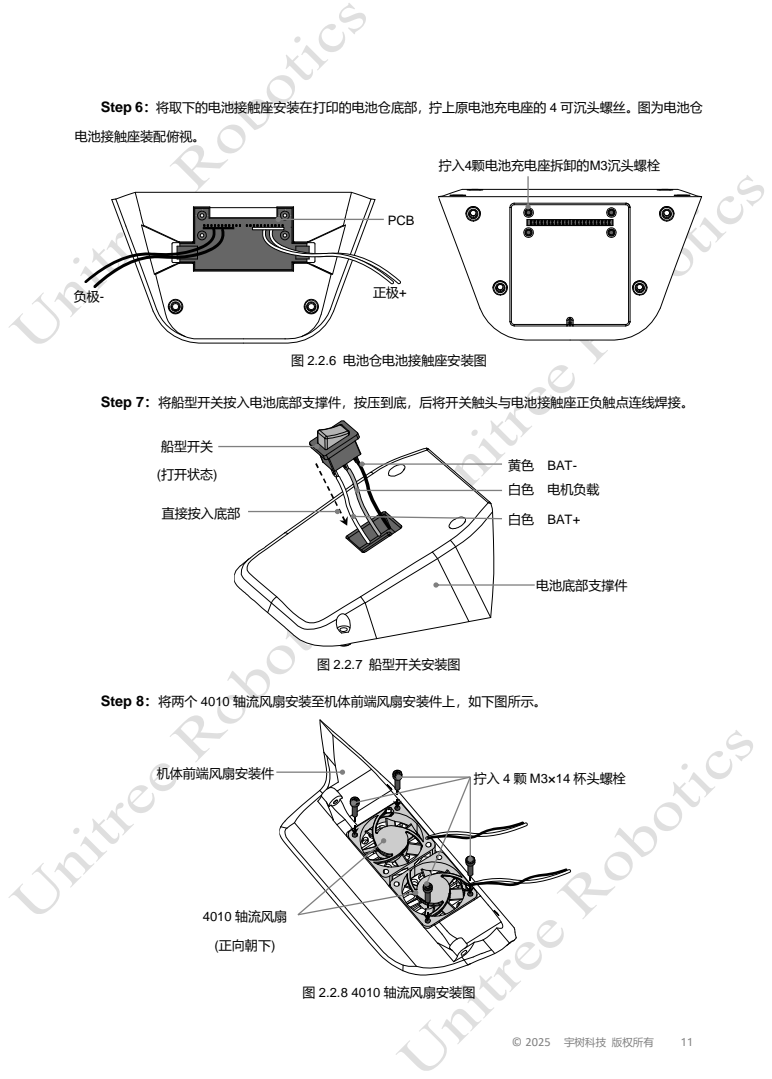
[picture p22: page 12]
电池接触座装配俯视。; 图 2.2.6 电池仓电池接触座安装图; 图 2.2.7 船型开关安装图; 图 2.2.8 4010 轴流风扇安装图; 拧入4颗电池充电座拆卸的M3沉头螺栓; PCB; 白色 BAT+; 黄色 BAT-; 船型开关; (打开状态); 电池底部支撑件; 直接按入底部; 白色 电机负载; 4010 轴流风扇; (正向朝下); 机体前端风扇安装件; 拧入 4 颗 M3×14 杯头螺栓

Step 6：将取下的电池接触座安装在打印的电池仓底部，拧上原电池充电座的 4 可沉头螺丝。图为电池仓

Step 7：将船型开关按入电池底部支撑件，按压到底，后将开关触头与电池接触座正负触点连线焊接。

Step 8：将两个 4010 轴流风扇安装至机体前端风扇安装件上，如下图所示。

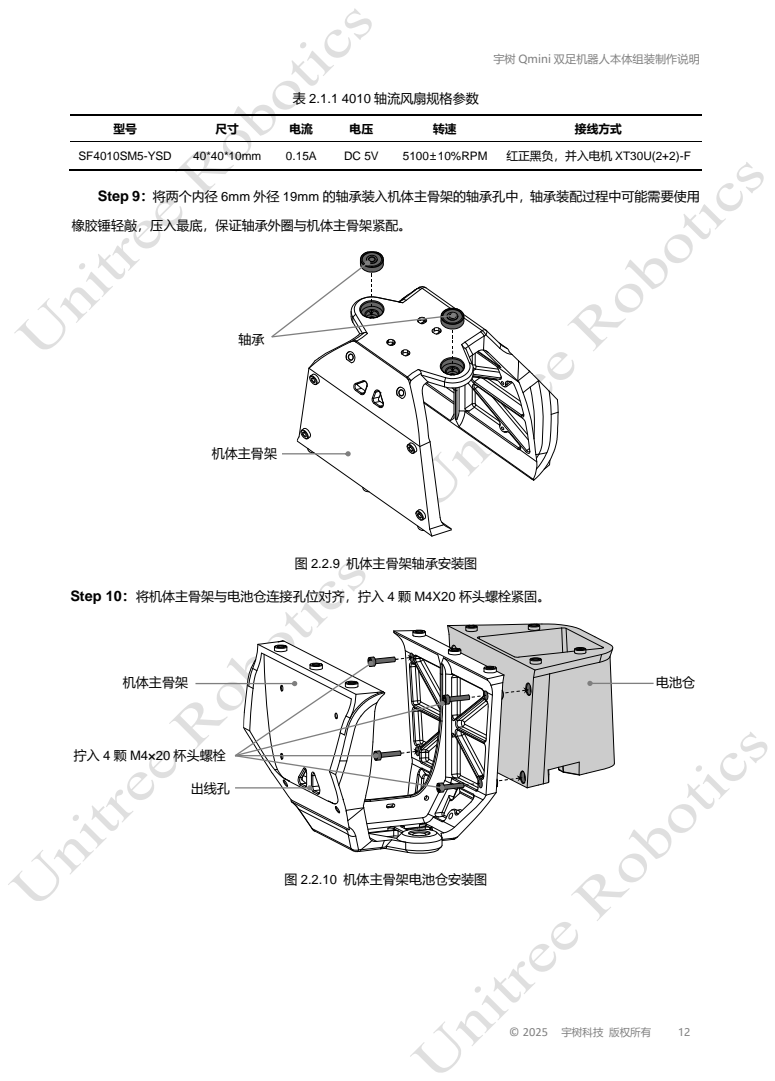
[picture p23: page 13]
表 2.1.1 4010 轴流风扇规格参数; 接线方式; SF4010SM5-YSD; 5100±10%RPM; 红正黑负，并入电机 XT30U(2+2)-F; 图 2.2.9 机体主骨架轴承安装图; 图 2.2.10 机体主骨架电池仓安装图; 机体主骨架; 拧入 4 颗 M4×20 杯头螺栓; 电池仓; 出线孔

Step 9：将两个内径 6mm 外径 19mm 的轴承装入机体主骨架的轴承孔中，轴承装配过程中可能需要使用

橡胶锤轻敲，压入最底，保证轴承外圈与机体主骨架紧配。

Step 10：将机体主骨架与电池仓连接孔位对齐，拧入 4 颗 M4X20 杯头螺栓紧固。

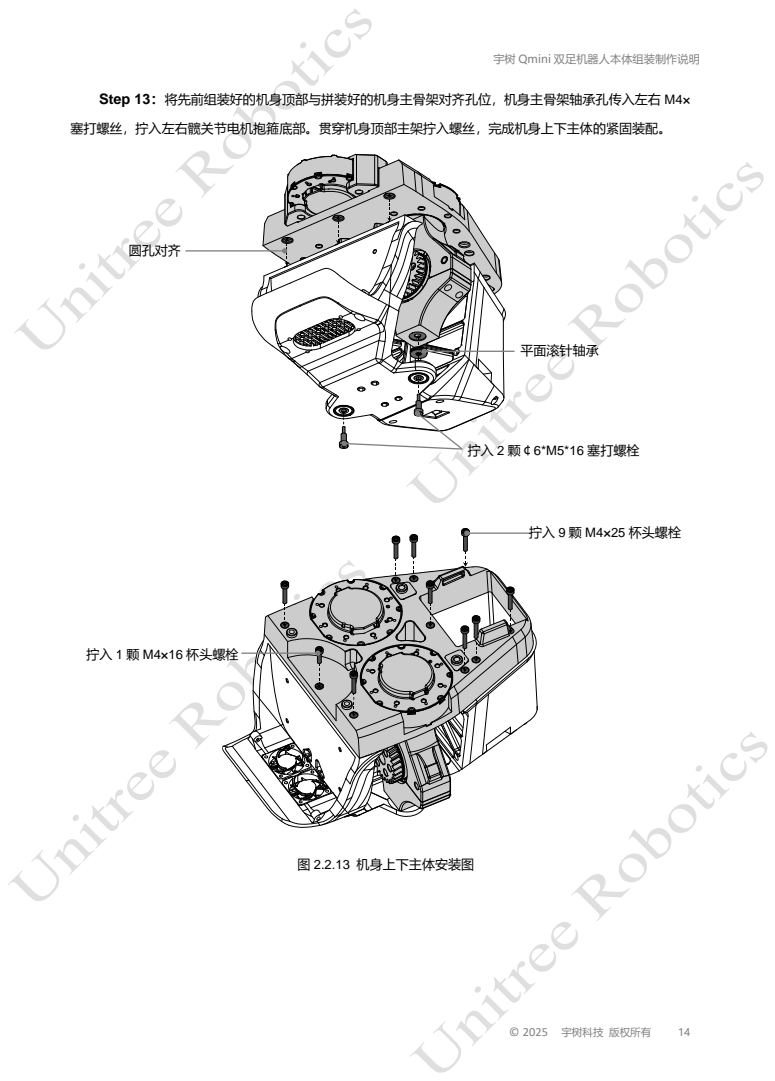
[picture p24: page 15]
图 2.2.13 机身上下主体安装图; 拧入 2 颗￠6*M5*16 塞打螺栓; 平面滚针轴承; 圆孔对齐; 拧入 9 颗 M4×25 杯头螺栓; 拧入 1 颗 M4×16 杯头螺栓

Step 13：将先前组装好的机身顶部与拼装好的机身主骨架对齐孔位，机身主骨架轴承孔传入左右 M4×

塞打螺丝，拧入左右髋关节电机抱箍底部。贯穿机身顶部主架拧入螺丝，完成机身上下主体的紧固装配。

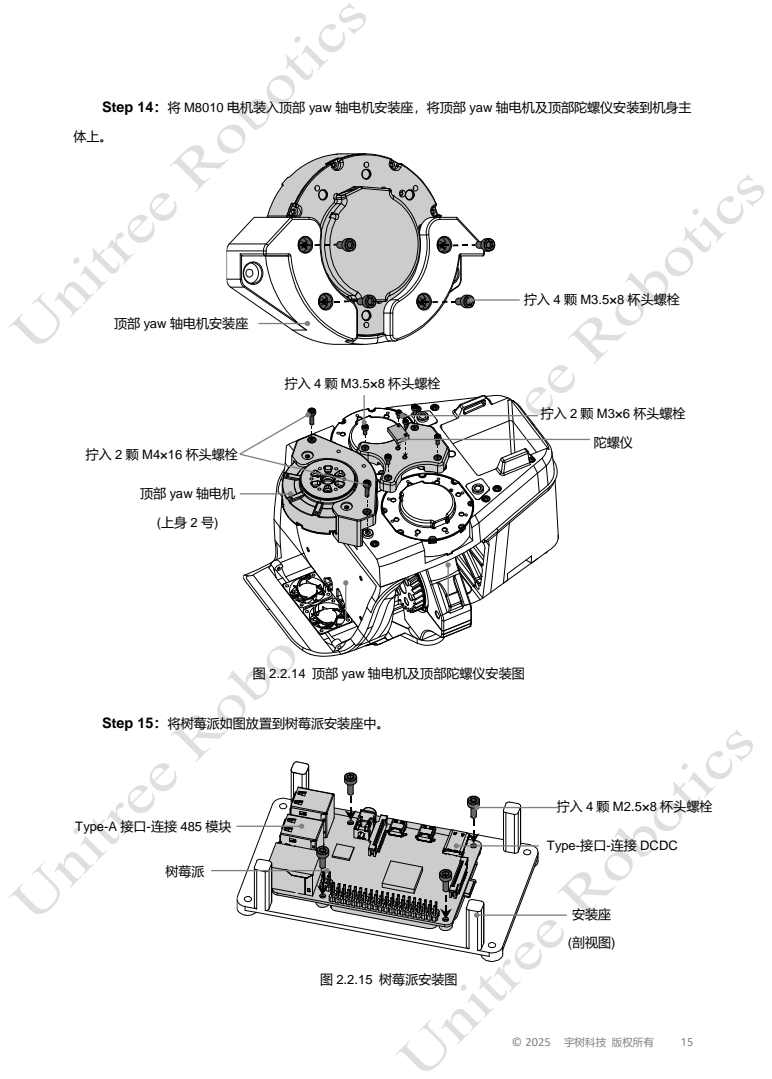
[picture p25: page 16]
Step 15：将树莓派如图放置到树莓派安装座中。; 图 2.2.15 树莓派安装图; 拧入 4 颗 M3.5×8 杯头螺栓; 拧入 2 颗 M4×16 杯头螺栓; 拧入 2 颗 M3×6 杯头螺栓; 陀螺仪; 拧入 4 颗 M2.5×8 杯头螺栓; 树莓派; 安装座; (剖视图)

Step 14：将 M8010 电机装入顶部 yaw 轴电机安装座，将顶部 yaw 轴电机及顶部陀螺仪安装到机身主

顶部 yaw 轴电机安装座

顶部 yaw 轴电机

图 2.2.14 顶部 yaw 轴电机及顶部陀螺仪安装图

Type-A 接口-连接 485 模块

Type-接口-连接 DCDC

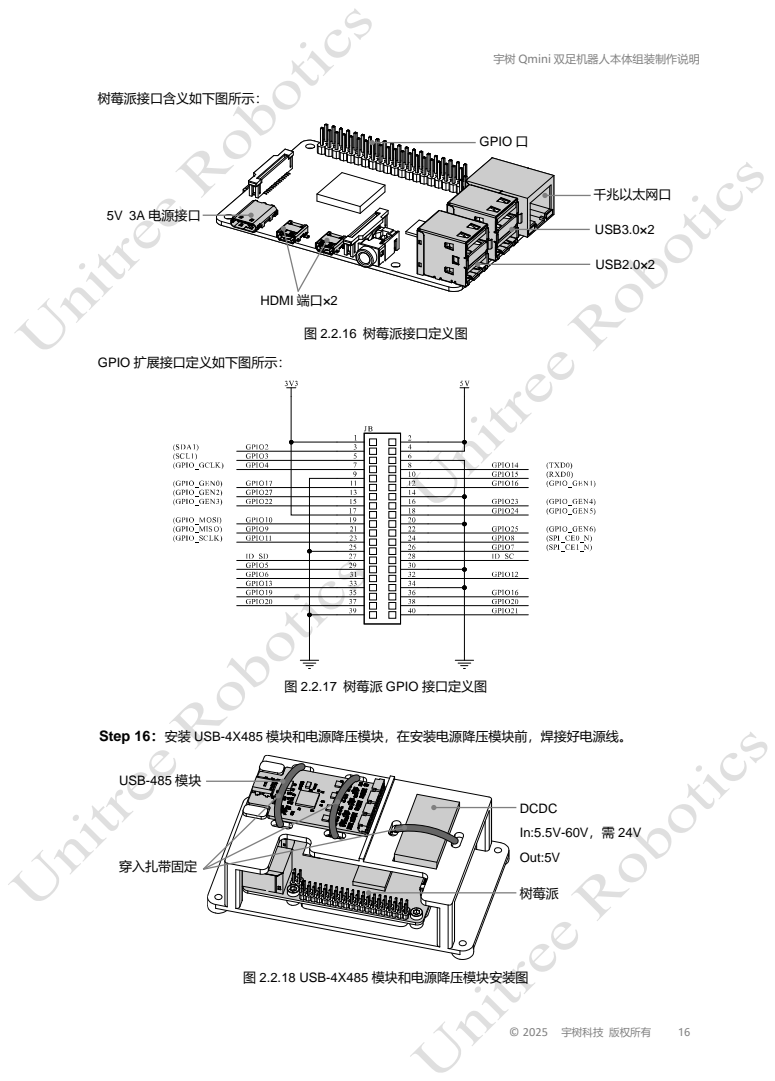
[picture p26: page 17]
树莓派接口含义如下图所示：; 图 2.2.16 树莓派接口定义图; GPIO 扩展接口定义如下图所示：; 图 2.2.18 USB-4X485 模块和电源降压模块安装图; 千兆以太网口; USB3.0×2; USB2.0×2; HDMI 端口×2; 5V 3A 电源接口; GPIO 口; DCDC; Out:5V; USB-485 模块; 穿入扎带固定; 树莓派

图 2.2.17 树莓派 GPIO 接口定义图

Step 16：安装 USB-4X485 模块和电源降压模块，在安装电源降压模块前，焊接好电源线。

电池受电板按照示意线序出线 2 正 2 负两组，两组均接入单刀单置船型开关触头，分别穿过机体主骨架下

方过线孔，一组接至 DCDC 输入，另一组接至上身 2 号（顶部 yaw 轴电机）。DCDC 输出接入树莓派电源输

⚫ 注意！！系统电源、电机 XT30 2+2-F 的线序定义，以免发生短路、断路等情况。

电机动力线：上身 2 号（顶部 yaw 轴电机）作为所有电机电源连接输入，上身 2 号至髋关节 1 号电机，髋

关节 1 号电机至髋关节 0 号电机，髋关节 0 号电机出线焊接连接成 T 字形结向上身 0 号电机、上身 1 号电机供

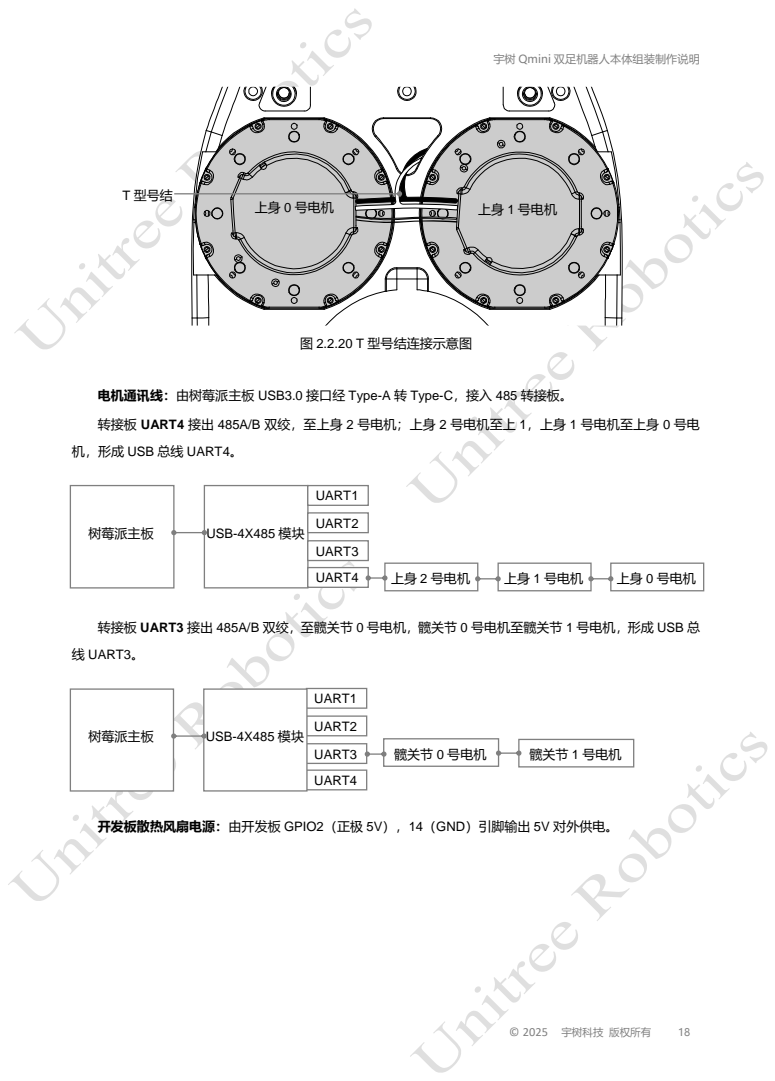
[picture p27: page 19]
图 2.2.20 T 型号结连接示意图; 线 UART3。; T 型号结; 上身 0 号电机; 上身 1 号电机; 树莓派主板; USB-4X485 模块; UART1; UART2; UART3; UART4; 上身 2 号电机; 髋关节 0 号电机; 髋关节 1 号电机

电机通讯线：由树莓派主板 USB3.0 接口经 Type-A 转 Type-C，接入 485 转接板。

转接板 UART4 接出 485A/B 双绞，至上身 2 号电机；上身 2 号电机至上 1，上身 1 号电机至上身 0 号电

机，形成 USB 总线 UART4。

转接板 UART3 接出 485A/B 双绞，至髋关节 0 号电机，髋关节 0 号电机至髋关节 1 号电机，形成 USB 总

开发板散热风扇电源：由开发板 GPIO2（正极 5V），14（GND）引脚输出 5V 对外供电。

## 2.2.3 机身整体安装效果

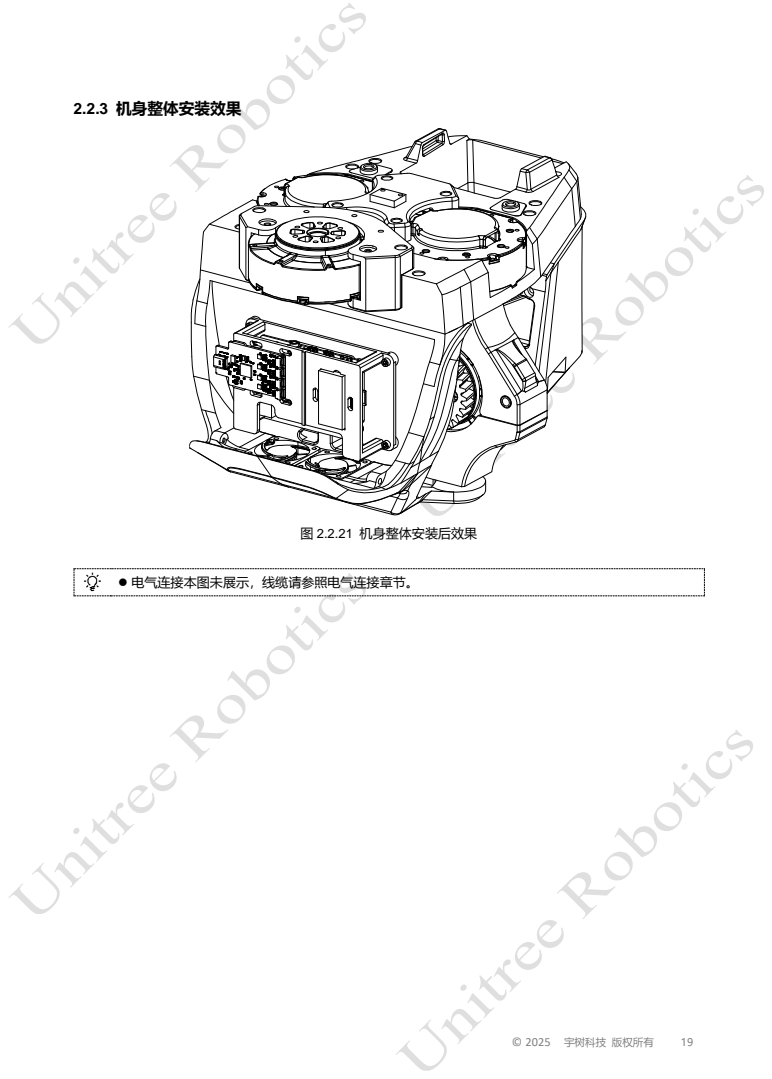
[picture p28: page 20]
图 2.2.21 机身整体安装后效果; ⚫ 电气连接本图未展示，线缆请参照电气连接章节。

## 2.3 腿部组装

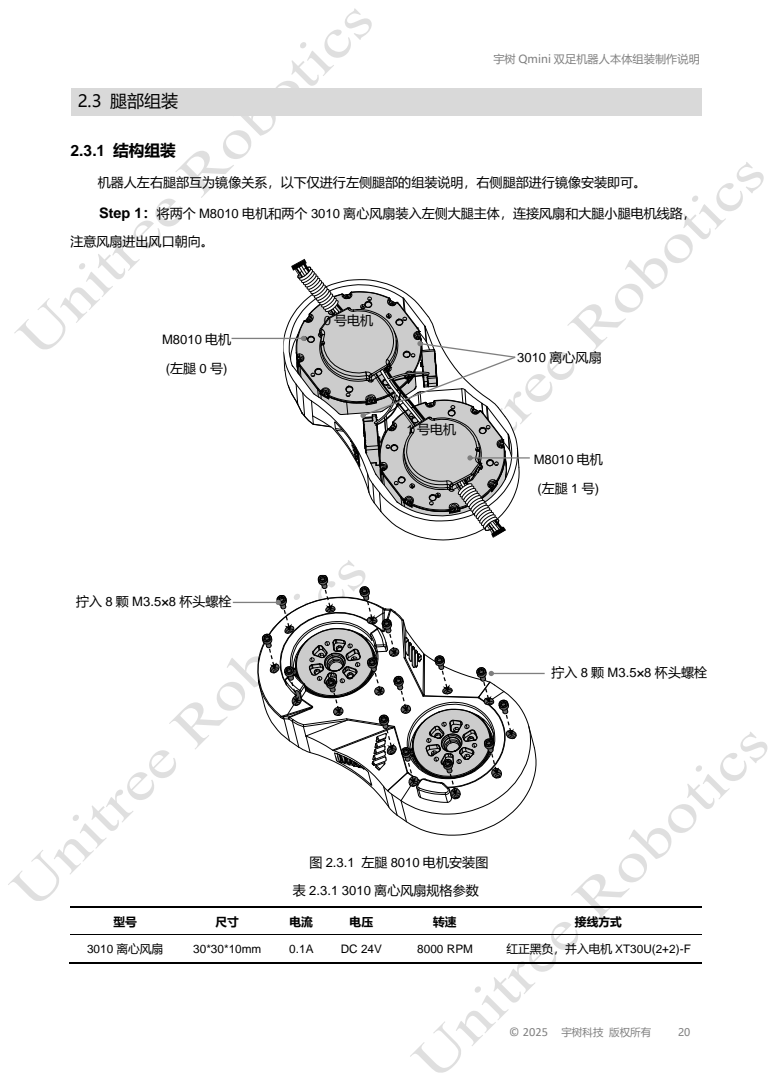
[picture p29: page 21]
2.3.1 结构组装; 注意风扇进出风口朝向。; 图 2.3.1 左腿 8010 电机安装图; 表 2.3.1 3010 离心风扇规格参数; 接线方式; 3010 离心风扇; 8000 RPM; 红正黑负，并入电机 XT30U(2+2)-F; 0 号电机; 1 号电机; 拧入 8 颗 M3.5×8 杯头螺栓

机器人左右腿部互为镜像关系，以下仅进行左侧腿部的组装说明，右侧腿部进行镜像安装即可。

Step 1：将两个 M8010 电机和两个 3010 离心风扇装入左侧大腿主体，连接风扇和大腿小腿电机线路，

Step 2：按照上图图示连接电机信号线后，盖上左侧大腿侧盖，盖上侧盖前，请确保保护线路的波纹管

Step 3：将一个 M8010 电机装入左侧小腿主体，如下图所示。

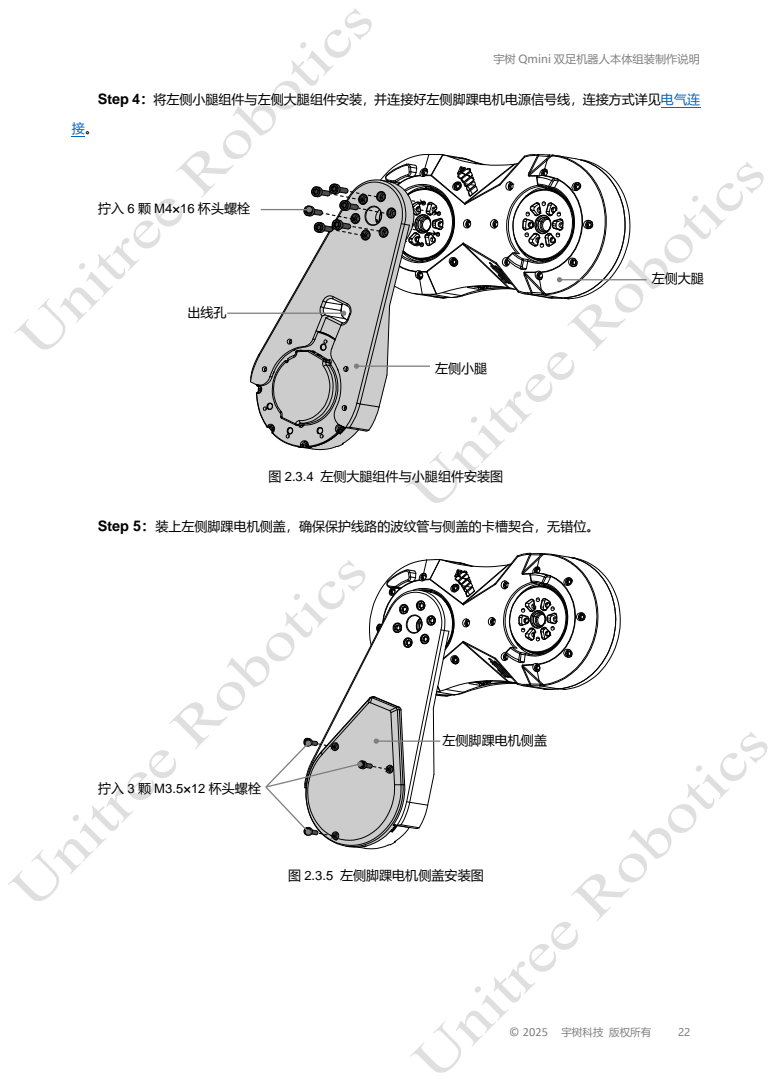
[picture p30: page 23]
图 2.3.4 左侧大腿组件与小腿组件安装图; 图 2.3.5 左侧脚踝电机侧盖安装图; 拧入 6 颗 M4×16 杯头螺栓; 左侧小腿; 左侧大腿; 出线孔; 拧入 3 颗 M3.5×12 杯头螺栓; 左侧脚踝电机侧盖

Step 4：将左侧小腿组件与左侧大腿组件安装，并连接好左侧脚踝电机电源信号线，连接方式详见电气连

Step 5：装上左侧脚踝电机侧盖，确保保护线路的波纹管与侧盖的卡槽契合，无错位。

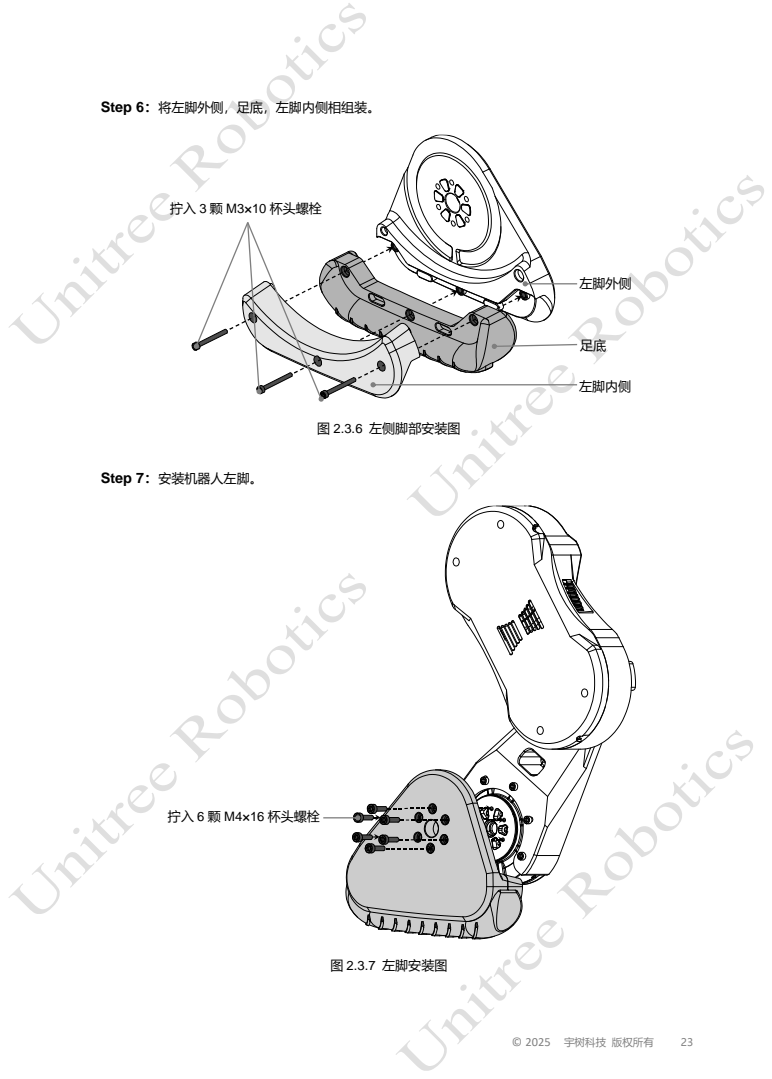
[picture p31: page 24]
图 2.3.6 左侧脚部安装图; Step 7：安装机器人左脚。; 图 2.3.7 左脚安装图; 拧入 3 颗 M3×10 杯头螺栓; 左脚内侧; 左脚外侧; 拧入 6 颗 M4×16 杯头螺栓

Step 6：将左脚外侧，足底，左脚内侧相组装。

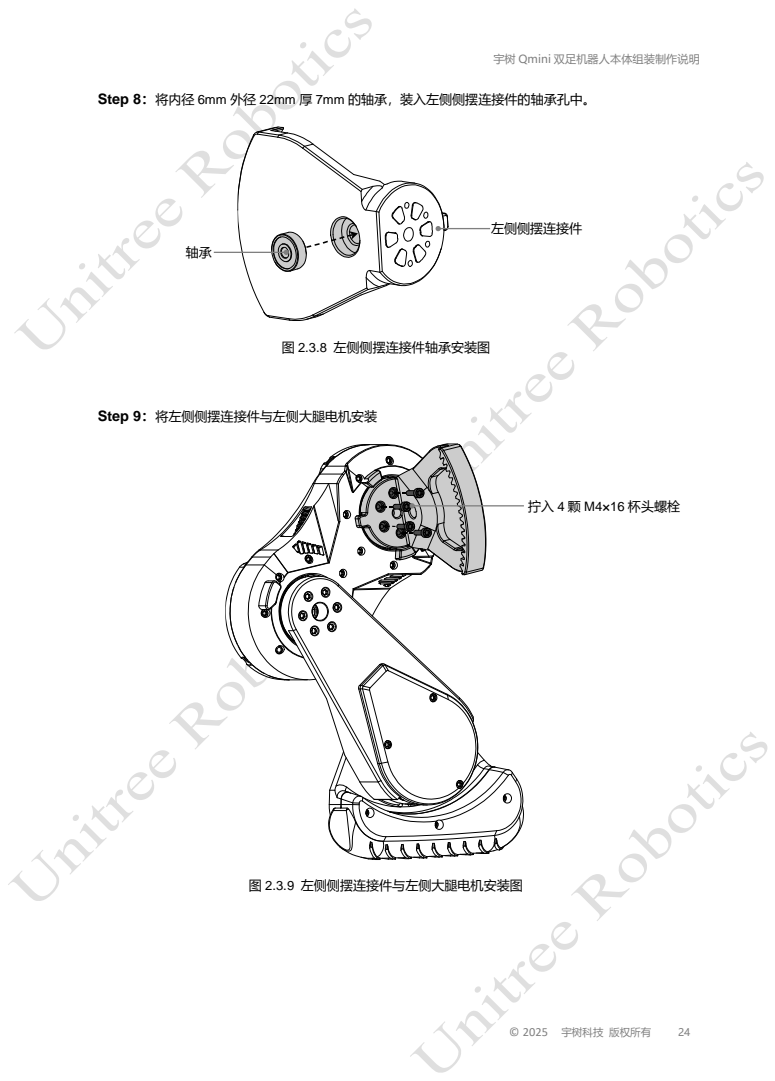
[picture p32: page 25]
图 2.3.8 左侧侧摆连接件轴承安装图; Step 9：将左侧侧摆连接件与左侧大腿电机安装; 图 2.3.9 左侧侧摆连接件与左侧大腿电机安装图; 左侧侧摆连接件; 拧入 4 颗 M4×16 杯头螺栓

Step 8：将内径 6mm 外径 22mm 厚 7mm 的轴承，装入左侧侧摆连接件的轴承孔中。

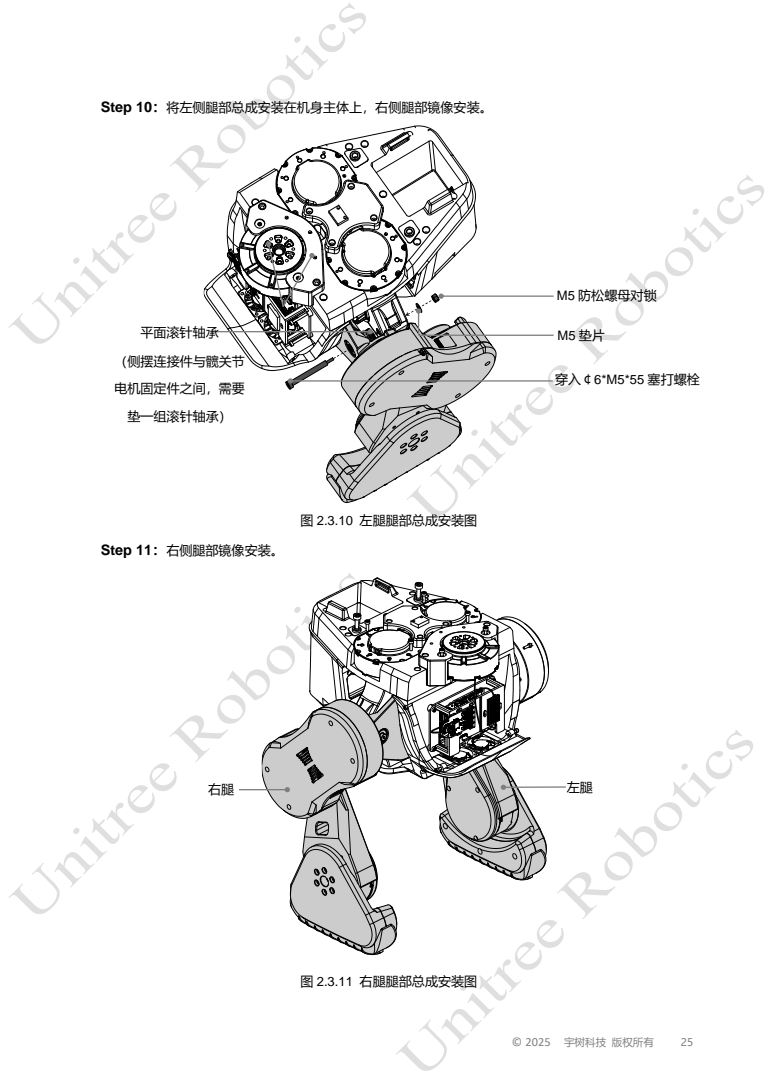
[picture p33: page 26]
图 2.3.10 左腿腿部总成安装图; Step 11：右侧腿部镜像安装。; 图 2.3.11 右腿腿部总成安装图; M5 防松螺母对锁; 平面滚针轴承; （侧摆连接件与髋关节; 电机固定件之间，需要; 垫一组滚针轴承）; 穿入￠6*M5*55 塞打螺栓

Step 10：将左侧腿部总成安装在机身主体上，右侧腿部镜像安装。

电机动力线：上身 0 号电机，至右腿 0 号电机，右腿 0 号电机至右腿 1 号电机，右腿 1 号电机至右腿 2 号

电机。上身 1 号电机，至左腿 0 号电机，左腿 0 号电机至左腿 1 号电机，左腿 1 号电机至左腿 2 号电机。

通讯线：由树莓派主板 USB3.0 接口经 Type-A 转 Type-C，接入 485 转接板。

转接板 UART2 接出 485A/B 双绞，至左腿 0，左腿 0 号电机至左腿 1 号电机，左腿 1 号电机至左腿 2 号

电机，形成 USB 总线 UART2。

转接板 UART1 接出 485A/B 双绞，至右腿 0 号电机，右腿 0 至右腿 1 号电机，右腿 1 至右腿 2 号电机，

形成 USB 总线 UART1。

腿部散热风扇电源：并入腿部电机 XT30 2+2 上供电。

## 2.3.3 腿部整体安装效果

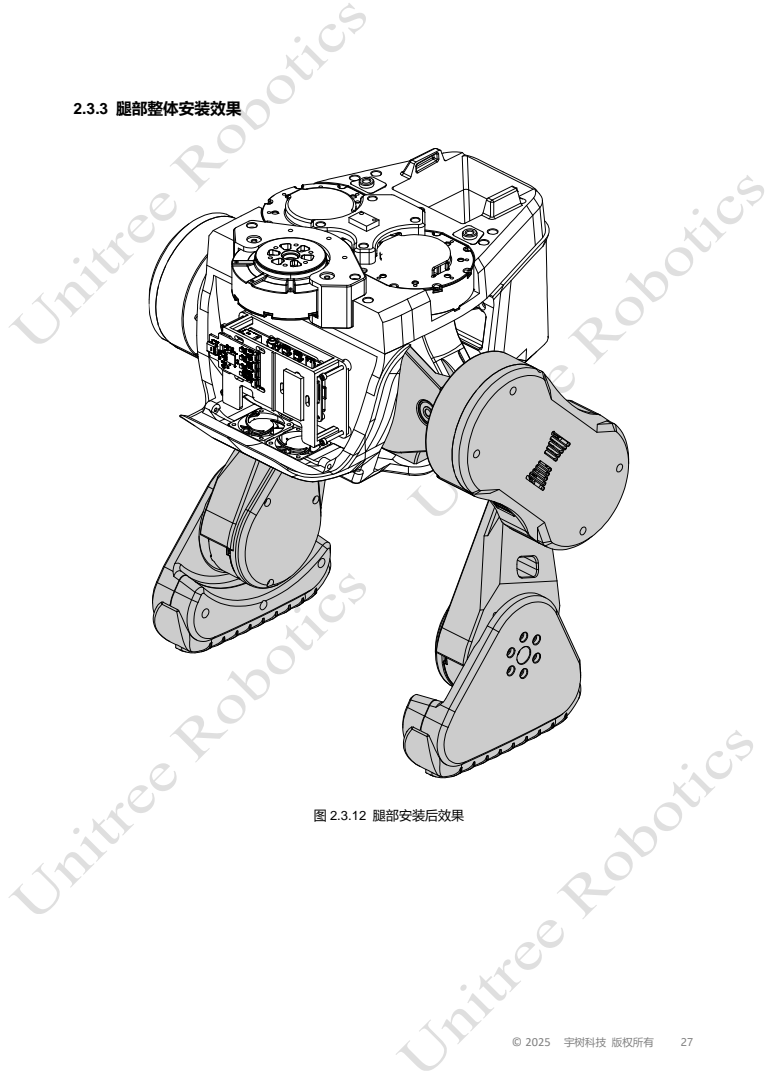
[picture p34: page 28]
图 2.3.12 腿部安装后效果

## 2.4 外观件组装

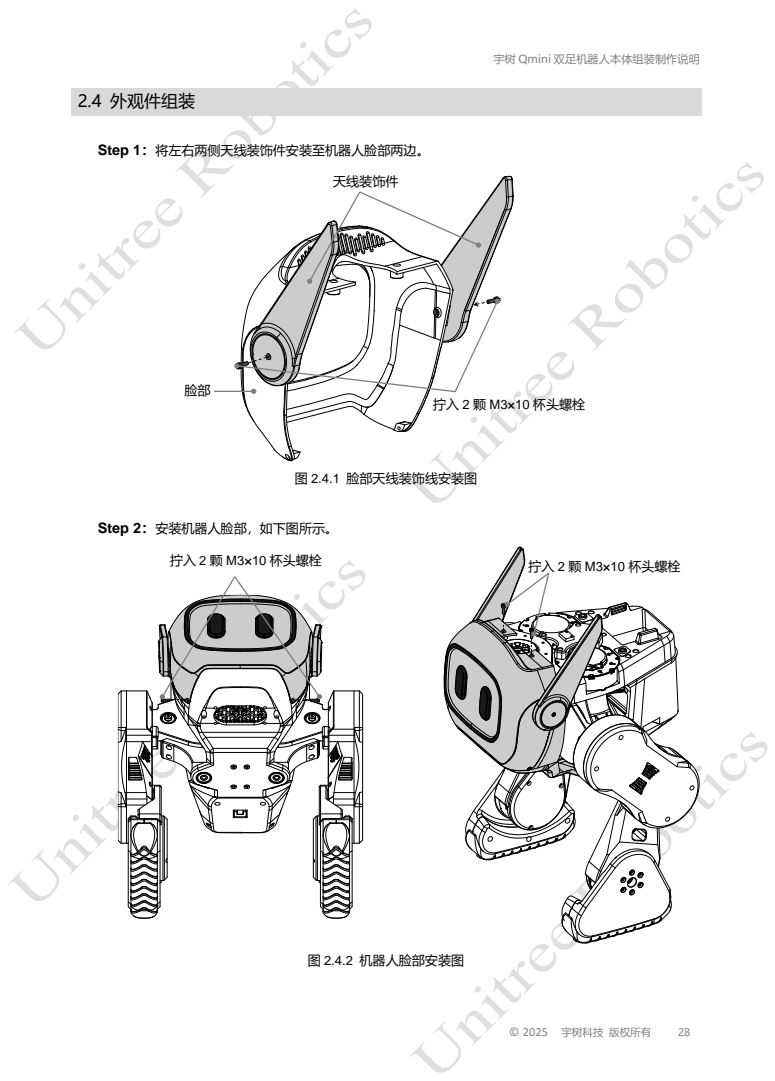
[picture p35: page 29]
Step 1：将左右两侧天线装饰件安装至机器人脸部两边。; 图 2.4.1 脸部天线装饰线安装图; 图 2.4.2 机器人脸部安装图; 拧入 2 颗 M3×10 杯头螺栓; 天线装饰件

Step 2：安装机器人脸部，如下图所示。

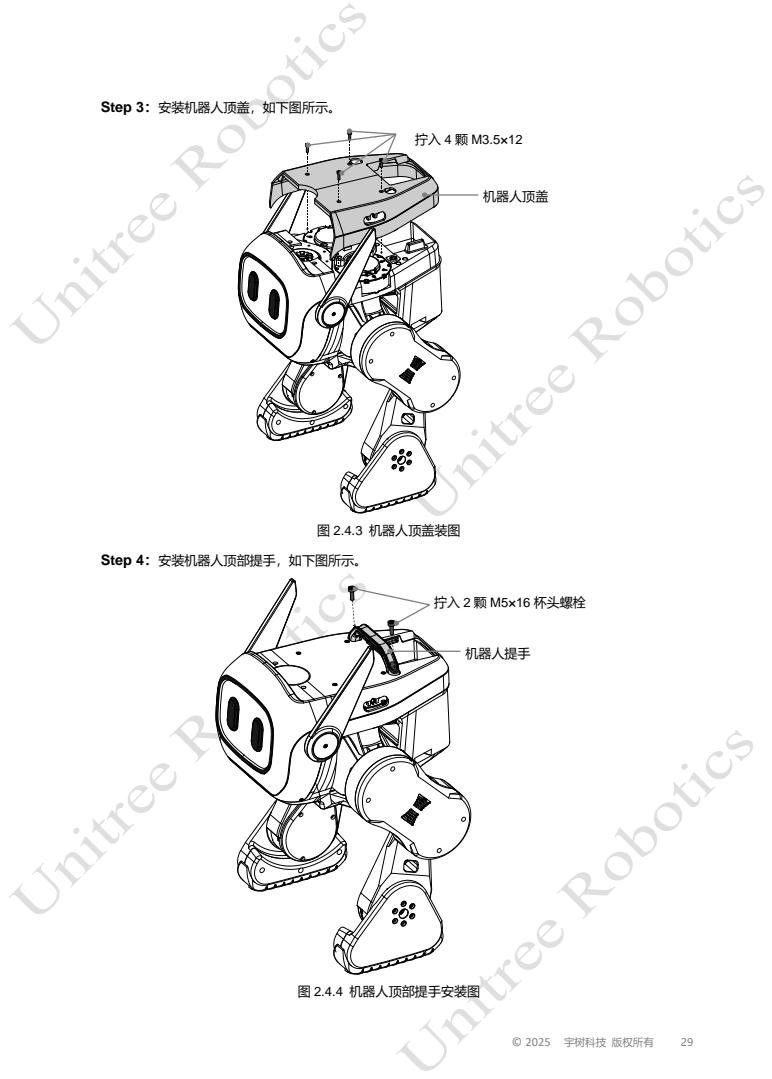
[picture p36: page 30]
图 2.4.3 机器人顶盖装图; 图 2.4.4 机器人顶部提手安装图; 机器人顶盖; 拧入 2 颗 M5×16 杯头螺栓; 机器人提手

Step 3：安装机器人顶盖，如下图所示。

Step 4：安装机器人顶部提手，如下图所示。

Step 5：安装电池，如下图所示。

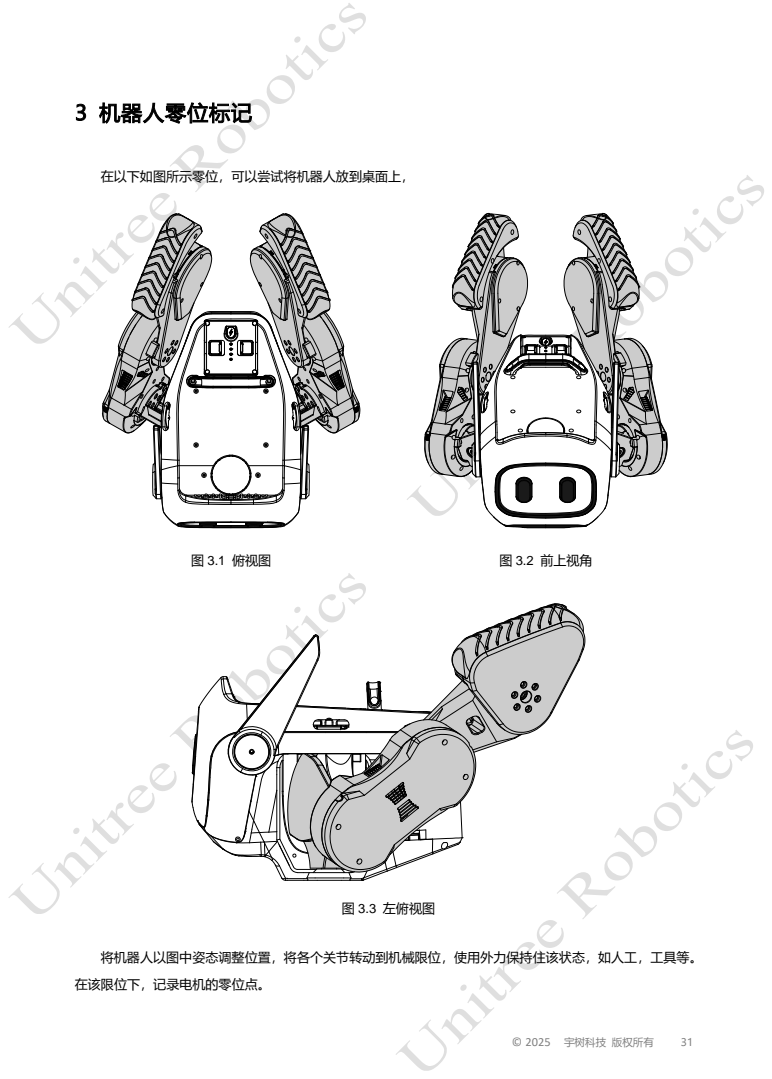
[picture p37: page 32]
在以下如图所示零位，可以尝试将机器人放到桌面上，; 图 3.1 俯视图; 图 3.2 前上视角; 图 3.3 左俯视图; 在该限位下，记录电机的零位点。

将机器人以图中姿态调整位置，将各个关节转动到机械限位，使用外力保持住该状态，如人工，工具等。

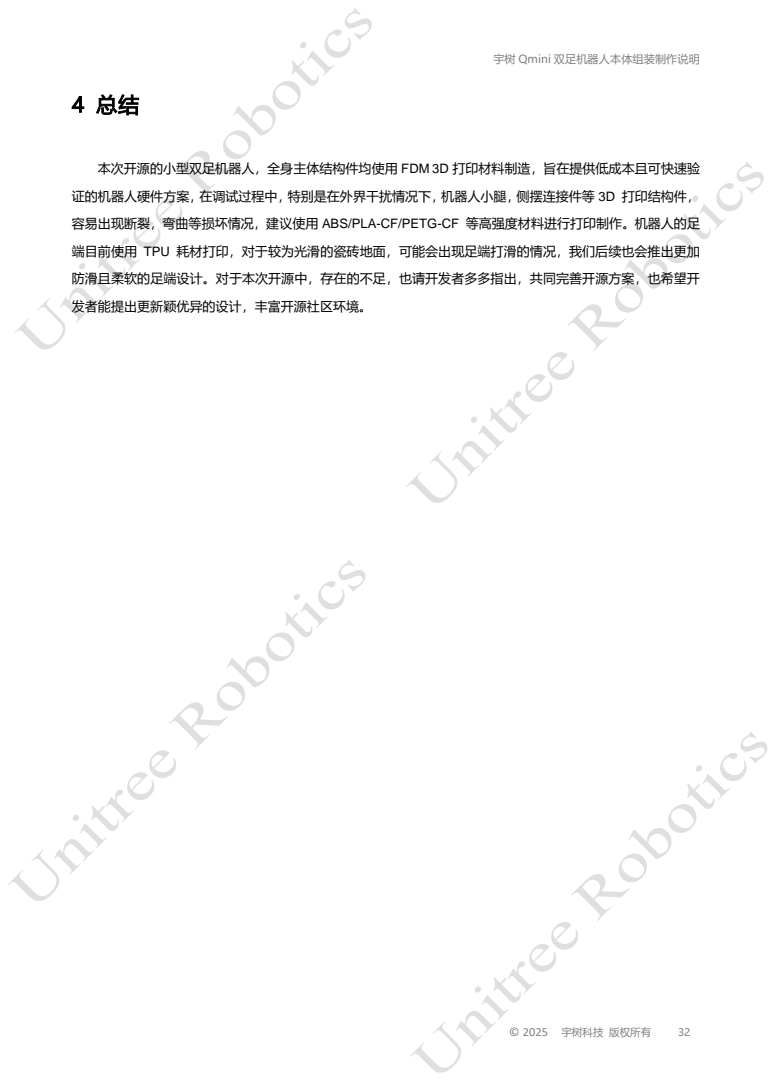
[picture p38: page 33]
发者能提出更新颖优异的设计，丰富开源社区环境。

本次开源的小型双足机器人，全身主体结构件均使用 FDM 3D 打印材料制造，旨在提供低成本且可快速验

证的机器人硬件方案，在调试过程中，特别是在外界干扰情况下，机器人小腿，侧摆连接件等 3D 打印结构件，

容易出现断裂，弯曲等损坏情况，建议使用 ABS/PLA-CF/PETG-CF 等高强度材料进行打印制作。机器人的足

端目前使用 TPU 耗材打印，对于较为光滑的瓷砖地面，可能会出现足端打滑的情况，我们后续也会推出更加

防滑且柔软的足端设计。对于本次开源中，存在的不足，也请开发者多多指出，共同完善开源方案，也希望开

https://www.unitree.com

您可以在 Unitree 官方网站获取更多文档

https://www.unitree.com/download

If you have any questions or suggestions about the manual, please contact us at the following

E-mail address: support@unitree.cc

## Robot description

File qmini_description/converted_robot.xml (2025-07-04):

<mujoco model="converted_robot">
  <compiler angle="radian" meshdir="meshes/"/>
  
  <asset>
    <texture name="groundplane" type="2d" builtin="checker" rgb1=".2 .3 .4" rgb2=".1 .2 .3" width="300" height="300" mark="cross" markrgb=".8 .8 .8"/>
    <material name="groundplane" texture="groundplane" texuniform="true" texrepeat="5 5" reflectance=".4"/>
    <mesh name="base_link" content_type="model/stl" file="base_link.STL"/>
    <mesh name="LL_hip_yaw" content_type="model/stl" file="LL_hip_yaw.STL"/>
    <mesh name="LL_hip_roll" content_type="model/stl" file="LL_hip_roll.STL"/>
    <mesh name="LL_hip_pitch" content_type="model/stl" file="LL_hip_pitch.STL"/>
    <mesh name="LL_knee" content_type="model/stl" file="LL_knee.STL"/>
    <mesh name="LL_ankle" content_type="model/stl" file="LL_ankle.STL"/>
    <mesh name="RL_hip_yaw" content_type="model/stl" file="RL_hip_yaw.STL"/>
    <mesh name="RL_hip_roll" content_type="model/stl" file="RL_hip_roll.STL"/>
    <mesh name="RL_hip_pitch" content_type="model/stl" file="RL_hip_pitch.STL"/>
    <mesh name="RL_knee" content_type="model/stl" file="RL_knee.STL"/>
    <mesh name="RL_ANKLE" content_type="model/stl" file="RL_ANKLE.STL"/>
  </asset>

  <worldbody>
    <geom name="ground" type="plane" size="10 10 0.1" rgba=".9 .9 .9 1" material="groundplane"/>
    <light directional="false" pos="0 1 1" dir="0 -1 -1" diffuse="1 1 1"/>
    <body name="base_link">
      <inertial pos="-0.014456 5.6e-05 -0.041502" quat="-0.00257562 0.606157 -0.00175674 0.795339" mass="4.7754" diaginertia="0.0508682 0.04973 0.0248209"/>
      <joint name="floating_base_joint" type="free" limited="false" actuatorfrclimited="false"/>
      <geom type="mesh" contype="0" conaffinity="0" group="1" density="0" rgba="1 1 1 1" mesh="base_link"/>
      <geom type="mesh" rgba="1 1 1 1" mesh="base_link"/>
      <body name="LL_hip_yaw" pos="0 0.055 0">
        <inertial pos="0.001558 0.000796 -0.10656" quat="0.999887 0.0135308 -0.0063304 0.00138268" mass="0.73407" diaginertia="0.00109609 0.000691105 0.000543803"/>
        <joint name="LL-joint1" pos="0 0 0" axis="0 0 1" range="-0.349 0.525" actuatorfrcrange="-20 20"/>
        <geom type="mesh" contype="0" conaffinity="0" group="1" density="0" rgba="1 1 1 1" mesh="LL_hip_yaw"/>
        <body name="LL_hip_roll" pos="0 0.054 -0.1073">
          <inertial pos="0.028723 -0.018625 1.5e-05" quat="0.704582 0.704582 0.0597045 0.0597045" mass="0.072409" diaginertia="0.000150731 0.000112 5.42688e-05"/>
          <joint name="LL-joint2" pos="0 0 0" axis="1 0 0" range="-0.275 0.698" actuatorfrcrange="-60 60"/>
          <geom type="mesh" contype="0" conaffinity="0" group="1" density="0" rgba="1 1 1 1" mesh="LL_hip_roll"/>
          <body name="LL_hip_pitch" pos="0.0165 0.028 0">
            <inertial pos="-0.040715 0.019181 -0.04067" quat="0.652202 0.271221 0.271606 0.653683" mass="1.4071" diaginertia="0.00653101 0.00572153 0.00111546"/>
            <joint name="LL-joint3" pos="0 0 0" axis="0 1 0" range="-0.61 1.483" actuatorfrcrange="-20 20"/>
            <geom type="mesh" contype="0" conaffinity="0" group="1" density="0" rgba="1 1 1 1" mesh="LL_hip_pitch"/>
            <geom type="mesh" rgba="1 1 1 1" mesh="LL_hip_pitch"/>
            <body name="LL_knee" pos="-0.081317 -0.0003 -0.081317">
              <inertial pos="0.048081 0.002331 -0.13228" quat="0.692133 -0.102953 -0.142857 0.69996" mass="0.76749" diaginertia="0.0018563 0.00143577 0.000554927"/>
              <joint name="LL-joint4" pos="0 0 0" axis="0 1 0" range="-1.117 1.047" actuatorfrcrange="-20 20"/>
              <geom type="mesh" contype="0" conaffinity="0" group="1" density="0" rgba="1 1 1 1" mesh="LL_knee"/>
              <geom type="mesh" rgba="1 1 1 1" mesh="LL_knee"/>
              <body name="LL_ankle" pos="0.053013 0.0228 -0.14565">
                <inertial pos="0.013735 -0.006344 -0.045775" quat="0.562412 0.442553 0.553176 0.426422" mass="0.2038" diaginertia="0.000663378 0.000494908 0.000224714"/>
                <joint name="LL-joint5" pos="0 0 0" axis="0 1 0" range="-1.396 1.221" actuatorfrcrange="-20 20"/>
                <geom type="mesh" contype="0" conaffinity="0" group="1" density="0" rgba="1 1 1 1" mesh="LL_ankle"/>
                <geom type="mesh" rgba="1 1 1 1" mesh="LL_ankle"/>
              </body>
            </body>
          </body>
        </body>
      </body>
      <body name="RL_hip_yaw" pos="0 -0.055 0">
        <inertial pos="0.001558 -0.000796 -0.10656" quat="0.999887 -0.0135308 -0.0063304 -0.00138268" mass="0.73407" diaginertia="0.00109609 0.000691105 0.000543803"/>
        <joint name="RL-joint1" pos="0 0 0" axis="0 0 1" range="-0.525 0.349" actuatorfrcrange="-20 20"/>
        <geom type="mesh" contype="0" conaffinity="0" group="1" density="0" rgba="1 1 1 1" mesh="RL_hip_yaw"/>
        <body name="RL_hip_roll" pos="0 -0.054 -0.1073">
          <inertial pos="0.028723 0.018625 1.5e-05" quat="0.704582 0.704582 -0.0597045 -0.0597045" mass="0.072409" diaginertia="0.000150731 0.000112 5.42688e-05"/>
          <joint name="RL-joint2" pos="0 0 0" axis="1 0 0" range="-0.698 0.275" actuatorfrcrange="-60 60"/>
          <geom type="mesh" contype="0" conaffinity="0" group="1" density="0" rgba="1 1 1 1" mesh="RL_hip_roll"/>
          <body name="RL_hip_pitch" pos="0.0165 -0.028 0">
            <inertial pos="-0.040715 -0.019181 -0.04067" quat="0.653683 0.271606 0.271221 0.652202" mass="1.4071" diaginertia="0.00653101 0.00572153 0.00111546"/>
            <joint name="RL-joint3" pos="0 0 0" axis="0 1 0" range="-0.61 1.483" actuatorfrcrange="-20 20"/>
            <geom type="mesh" contype="0" conaffinity="0" group="1" density="0" rgba="1 1 1 1" mesh="RL_hip_pitch"/>
            <geom type="mesh" rgba="1 1 1 1" mesh="RL_hip_pitch"/>
            <body name="RL_knee" pos="-0.081317 0.0003 -0.081317">
              <inertial pos="0.048081 -0.002331 -0.13228" quat="0.69996 -0.142857 -0.102953 0.692133" mass="0.76749" diaginertia="0.0018563 0.00143577 0.000554927"/>
              <joint name="RL-joint4" pos="0 0 0" axis="0 1 0" range="-1.117 1.047" actuatorfrcrange="-20 20"/>
              <geom type="mesh" contype="0" conaffinity="0" group="1" density="0" rgba="1 1 1 1" mesh="RL_knee"/>
              <geom type="mesh" rgba="1 1 1 1" mesh="RL_knee"/>
              <body name="RL_ANKLE" pos="0.053013 -0.0228 -0.14565">
                <inertial pos="0.013735 0.006344 -0.045775" quat="0.426422 0.553176 0.442553 0.562412" mass="0.2038" diaginertia="0.000663378 0.000494908 0.000224714"/>
                <joint name="RL-joint5" pos="0 0 0" axis="0 1 0" range="-1.396 1.221" actuatorfrcrange="-20 20"/>
                <geom type="mesh" contype="0" conaffinity="0" group="1" density="0" rgba="1 1 1 1" mesh="RL_ANKLE"/>
                <geom type="mesh" rgba="1 1 1 1" mesh="RL_ANKLE"/>
              </body>
            </body>
          </body>
        </body>
      </body>
    </body>
  </worldbody>
</mujoco>

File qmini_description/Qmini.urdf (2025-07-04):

<robot name="Qmini">
  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
  <link name="base_link">
    <inertial>
      <origin xyz="-0.014456 5.6E-05 -0.041502" rpy="0 0 0"/>
      <mass value="4.7754"/>
      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
    </inertial>
    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
  </link>
  <link name="LL_hip_yaw">
    <inertial>
      <origin xyz="0.001558 0.000796 -0.10656" rpy="0 0 0"/>
      <mass value="0.73407"/>
      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
    </inertial>
    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
  </link>
  <joint name="LL-joint1" type="revolute">
    <origin xyz="0 0.055 0" rpy="0 0 0"/>
    <parent link="base_link"/>
    <child link="LL_hip_yaw"/>
    <axis xyz="0 0 1"/>
    <limit lower="-0.349" upper="0.525" effort="20" velocity="1"/>
  </joint>
  <link name="LL_hip_roll">
    <inertial>
      <origin xyz="0.028723 -0.018625 1.5E-05" rpy="0 0 0"/>
      <mass value="0.072409"/>
      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
    </inertial>
    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
  </link>
  <joint name="LL-joint2" type="revolute">
    <origin xyz="0 0.054 -0.1073" rpy="0 0 0"/>
    <parent link="LL_hip_yaw"/>
    <child link="LL_hip_roll"/>
    <axis xyz="1 0 0"/>
    <limit lower="-0.275" upper="0.698" effort="60" velocity="0.3"/>
  </joint>
  <link name="LL_hip_pitch">
    <inertial>
      <origin xyz="-0.040715 0.019181 -0.04067" rpy="0 0 0"/>
      <mass value="1.4071"/>
      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
    </inertial>
    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
  </link>
  <joint name="LL-joint3" type="revolute">
    <origin xyz="0.0165 0.028 0" rpy="0 0 0"/>
    <parent link="LL_hip_roll"/>
    <child link="LL_hip_pitch"/>
    <axis xyz="0 1 0"/>
    <limit lower="-0.61" upper="1.483" effort="20" velocity="1"/>
  </joint>
  <link name="LL_knee">
    <inertial>
      <origin xyz="0.048081 0.002331 -0.13228" rpy="0 0 0"/>
      <mass value="0.76749"/>
      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
    </inertial>
    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
  </link>
  <joint name="LL-joint4" type="revolute">
    <origin xyz="-0.081317 -0.0003 -0.081317" rpy="0 0 0"/>
    <parent link="LL_hip_pitch"/>
    <child link="LL_knee"/>
    <axis xyz="0 1 0"/>
    <limit lower="-1.117" upper="1.047" effort="20" velocity="1"/>
  </joint>
  <link name="LL_ankle">
    <inertial>
      <origin xyz="0.013735 -0.006344 -0.045775" rpy="0 0 0"/>
      <mass value="0.2038"/>
      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
    </inertial>
    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
  </link>
  <joint name="LL-joint5" type="revolute">
    <origin xyz="0.053013 0.0228 -0.14565" rpy="0 0 0"/>
    <parent link="LL_knee"/>
    <child link="LL_ankle"/>
    <axis xyz="0 1 0"/>
    <limit lower="-1.396" upper="1.221" effort="20" velocity="1"/>
  </joint>
  <link name="RL_hip_yaw">
    <inertial>
      <origin xyz="0.001558 -0.000796 -0.10656" rpy="0 0 0"/>
      <mass value="0.73407"/>
      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
    </inertial>
    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
  </link>
  <joint name="RL-joint1" type="revolute">
    <origin xyz="0 -0.055 0" rpy="0 0 0"/>
    <parent link="base_link"/>
    <child link="RL_hip_yaw"/>
    <axis xyz="0 0 1"/>
    <limit lower="-0.525" upper="0.349" effort="20" velocity="1"/>
  </joint>
  <link name="RL_hip_roll">
    <inertial>
      <origin xyz="0.028723 0.018625 1.5E-05" rpy="0 0 0"/>
      <mass value="0.072409"/>
      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
    </inertial>
    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
  </link>
  <joint name="RL-joint2" type="revolute">
    <origin xyz="0 -0.054 -0.1073" rpy="0 0 0"/>
    <parent link="RL_hip_yaw"/>
    <child link="RL_hip_roll"/>
    <axis xyz="1 0 0"/>
    <limit lower="-0.698" upper="0.275" effort="60" velocity="0.3"/>
  </joint>
  <link name="RL_hip_pitch">
    <inertial>
      <origin xyz="-0.040715 -0.019181 -0.04067" rpy="0 0 0"/>
      <mass value="1.4071"/>
      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
    </inertial>
    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
  </link>
  <joint name="RL-joint3" type="revolute">
    <origin xyz="0.0165 -0.028 0" rpy="0 0 0"/>
    <parent link="RL_hip_roll"/>
    <child link="RL_hip_pitch"/>
    <axis xyz="0 1 0"/>
    <limit lower="-0.61" upper="1.483" effort="20" velocity="1"/>
  </joint>
  <link name="RL_knee">
    <inertial>
      <origin xyz="0.048081 -0.002331 -0.13228" rpy="0 0 0"/>
      <mass value="0.76749"/>
      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
    </inertial>
    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
  </link>
  <joint name="RL-joint4" type="revolute">
    <origin xyz="-0.081317 0.0003 -0.081317" rpy="0 0 0"/>
    <parent link="RL_hip_pitch"/>
    <child link="RL_knee"/>
    <axis xyz="0 1 0"/>
    <limit lower="-1.117" upper="1.047" effort="20" velocity="1"/>
  </joint>
  <link name="RL_ankle">
    <inertial>
      <origin xyz="0.013735 0.006344 -0.045775" rpy="0 0 0"/>
      <mass value="0.2038"/>
      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
    </inertial>
    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
  </link>
  <joint name="RL-joint5" type="revolute">
    <origin xyz="0.053013 -0.0228 -0.14565" rpy="0 0 0"/>
    <parent link="RL_knee"/>
    <child link="RL_ankle"/>
    <axis xyz="0 1 0"/>
    <limit lower="-1.396" upper="1.221" effort="20" velocity="1"/>
  </joint>
</robot>

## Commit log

2025-05-23 Update STLs
    [Battery Pack.stl, Hip Gear Left.stl, Hip Gear Right.stl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]
2025-05-23 Create Frame Top.stl
    [Frame Top.stl]
2025-05-23 Add Unitree Qmini V1.0 STEP
    [Unitree Qmini V1.0.step]
2025-05-23 Commit Panels
    [Panel Front.stl, Panel Top.stl]
2025-05-24 Create Raspberry Pi 4B Mount.stl
    [Raspberry Pi 4B Mount.stl]
2025-05-26 Create Qmini Printing Hours.xlsx
    [Qmini Printing Hours.xlsx]
2025-05-26 Organize file folders
    [Left Foot A.stl, Left Foot B.stl, Lower Leg Left Cover.stl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]
2025-05-26 Update Qmini Printing Hours.xlsx
    [Qmini Printing Hours.xlsx]
2025-05-26 Update spreadsheet
    [Qmini Printing Hours.xlsx]
2025-05-26 Update foot chamfer
    [Left Foot B.stl, Right Foot B.stl]
2025-05-26 Better for supportless
    [Left Foot A.stl, Right Foot A.stl]
2025-05-28 Update BOM
    [BOM.xlsx, Qmini Printing Hours.xlsx]
2025-05-29 Update Yaw Top.stl
    [Yaw Top.stl]
2025-06-01 Update Legs
    [Hollow - Lower Leg Left Cover.stl, Hollow - Lower Leg Right Cover.stl, Lower Leg Left Cover Test.stl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]
2025-06-03 Update Panel Top Rear.stl
2025-06-18 Update Panel
    [Panel Top Rear.3mf]
2025-06-22 Update KCD1-104 switch
    [BOM.xlsx]
2025-06-22 Create IMU N100 Mount.stl
    [IMU N100 Mount.stl]
2025-06-22 Commit Jetson Orin Nano
    [Jetson Orin Nano Mount A.stl, Jetson Orin Nano Mount B.stl]
2025-06-23 Commit standing frame files
    [Left Foot Holder.3mf, Main Frame.3mf, Right Foot Holder.3mf]
2025-06-23 Commit standing frame BOM
    [BOM.xlsx]
2025-06-24 Commit battery pack for DJI TB50 with 4010 DC 24V cooling fan
    Folders reorganized
    [Battery Pack Bottom GO1.stl, Battery Pack Bottom with 4010 Fan.stl, Battery Pack GO1.stl]
2025-06-24 Update IMU N100 Mount.stl
    [IMU N100 Mount.stl]
2025-07-04 Commit Qmini URDF
    [LL_ankle.STL, LL_hip_pitch.STL, LL_hip_roll.STL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]
2025-07-04 Commit qmini_description for ROS2
    [LL_ankle.STL, LL_hip_pitch.STL, LL_hip_roll.STL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]
2025-07-11 Extend standing frame for better standing legs position
    [Main Frame.3mf, Standing Frame A.stl, Standing Frame B.stl]
2025-07-23 Create Stand Base.3mf
    [Stand Base.3mf]
2025-07-29 Commit Qmini charger PCB board
    [qmini-battery.GBL, qmini-battery.GBO, qmini-battery.GBP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]
2025-08-17 Create Qmini - Bambu Studio.3mf
    [Qmini - Bambu Studio.3mf]
2025-09-19 Update Qmini - Bambu Studio.3mf
    [Qmini - Bambu Studio.3mf]
